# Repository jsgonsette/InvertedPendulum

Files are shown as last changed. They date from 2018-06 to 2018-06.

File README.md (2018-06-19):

# Inverted Pendulum

**Wanna build an inverted pendulum ?** Like in this video :

Pendulum movie (https://www.youtube.com/watch?v=6xe19XnX5L0&t=20s)

you are in the right place. All what you need to known to get an incredible pendulum that jumps and balances is available here. I describe:

* how to make the *electronic board*
* how to make the *shell*
* how to get the *other components*
* how to program the *firmware*
* how to *assemble* the pendulum
* how to connect to the *Control Station software*
* how to *calibrate* the sensors

If you understand french, the long way explanation can be found [on my blog](https://jsgonsette.github.io/). Otherwise, keep reading.

## How to make the electronic board

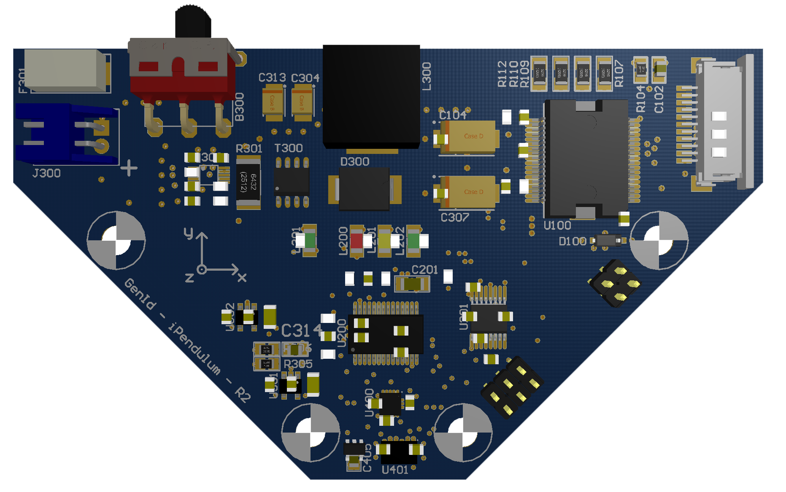
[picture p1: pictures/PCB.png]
Pendulum PCB


### Get the BOM
First, you need all the electronic components on this [BOM list](./Electronic/BOM.xlsx). This kind of components can be found on different sites like:

* [Farnell](http://farnell.com/)
* [RS Components](http://www.rs-online.com/)
* [DigiKey](https://www.digikey.com/)

### Make the PCB
You need to make the PCB whose plans are given by the different files in this [directory](./Electronic/PCB).
(To be continued)

### Soldering of the components

Refer to this [implementation plan](./Electronic/PCB/PCB.PDF) to solder the different components on the both faces. With enough dexterity and patience, all the components could be soldered by hand with a soldering iron. **There are two exceptions**:

* U400 and U401 are only available in LGA package, which means: **no weldable legs !**

You have two options for those ones:

* either you are confident enough to use solder paste and an oven ;
* or you do it like me and you ask your PCB manufacturer to do it for you. This option is ofen available and you can save money by asking them to only solder those two components.

## How to make the shell

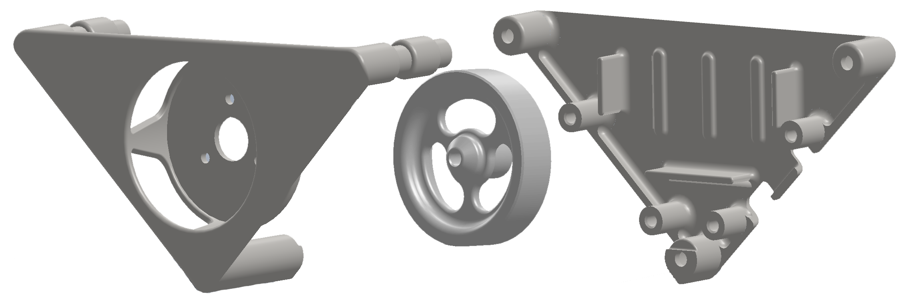
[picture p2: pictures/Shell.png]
Pendulum shell


The shell of the pendulum is composed of three pieces, whose plans are given by the three STEP files in this [directory](./Mecanic/Shell)

* Back of the shell, holding the PCB and the battery
* Front of the shell, holding the motor
* The hub of the flywheel

They have to be 3D printed. You can do it yourself in case you have access to a 3D printer, or just use an online service like [Sculpteo](https://www.sculpteo.com). You need to upload the three STEP files, then to chose this material: [Nylon PA12 (Plastic)](https://www.sculpteo.com/en/materials/plastic-material/). Don't go to other materials, as it could change the weight of the pendulum ; **weight is important!**

## How to get the other components

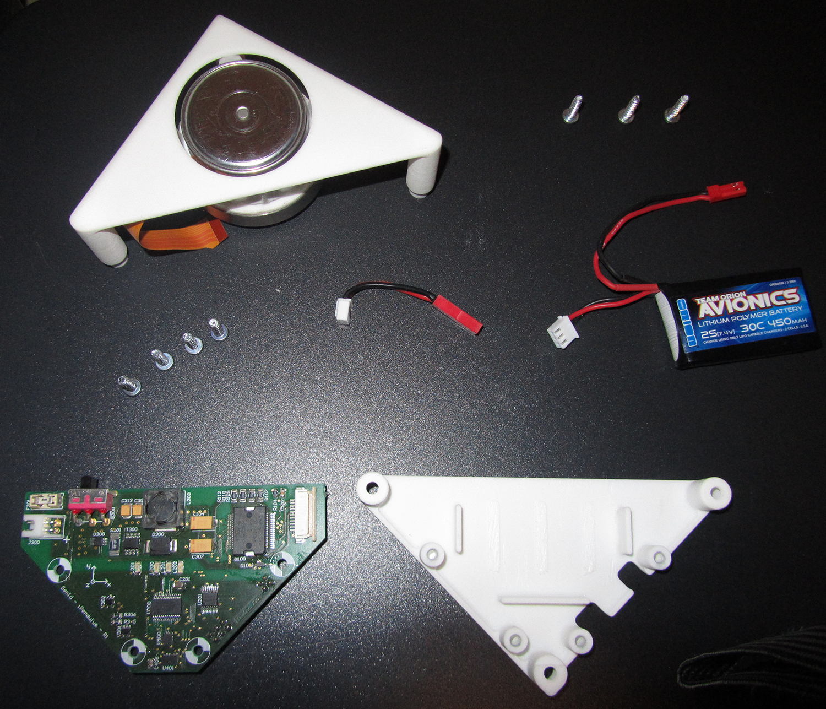
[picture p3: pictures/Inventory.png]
Pendulum inventory


Some additional parts are still needed before getting a functional pendulum.

* The metallic outer ring of the flywheel. It can be ordered on the [Misumi web site](https://uk.misumi-ec.com/). Use the reference **AWSM-D-D55-V48-T10** in the search box to land on the right page.
* The Maxon brushless motor whose reference is [EC45 Flat 200142](https://www.maxonmotor.com/maxon/view/product/200142), available on RS.
* The Lipo battery. The model is not so important, as long as the physical dimensions and the output voltage are respectively: 5x3x1cm and 7.5V. A possible choice can be found [here](https://www.guixmodel.fr/modelisme/accus-et-chargeurs/accus/lipo-2s/accu-lipo-450mah-2s-30c-kryptonium-detail).
* Seven screws to atttach the PCB in the shell and to tie the two parts of the shell together. Check this [Assembly BOM](Assembly%20BOM.xlsx).
* Three screws to attache the motor in the shell. Check this [Assembly BOM](Assembly%20BOM.xlsx).
* The cable to connect the PCB to the battery. You have to assemble it yourself. Check this [Cables BOM](./Mecanic/Cables%20BOM.xlsx).
* The cable to connect the pendulum to the PIC microcontroller programmer. You have to assemble it yourself. Check this [Cables BOM](./Mecanic/Cables%20BOM.xlsx).
* A Lipo charger. Personnaly, I'm very pleased with the [Graupner UltraMat 14 plus](https://www.graupner.de/mediaroot/files/6464_Ultramat_14_plus_de_en_fr_it.pdf) but there are many other ones.
* A Microchip programmation device like the [PICkit 3](https://www.microchip.com/Developmenttools/ProductDetails/PG164130) or the [ICD 3](https://www.microchip.com/Developmenttools/ProductDetails/DV164035), availabe on Farnell, for example.
* (optional) The cable to connect the pendulum to a serial cable. You have to assemble it yourself. Check this [Cables BOM](./Mecanic/Cables%20BOM.xlsx).
* (optional) a USB - Serial cable

## How to program the firmware

The brain of the pendulum is a small Microchip 16bits µC. You must load the right firmware inside to give life to the pendulum.

* Download and install [Microchip MPLAB X](http://microchipdeveloper.com/ipe:installation)
* Connect your chip programmer (like the PICkit 3 or the ICD 3) to the electonic board P200 connector with the dedicated cable
* Connect your chip programmer to your computer
* Charge the Lipo battery and connect it to the electronic board
* Power up the electronic board by switching the power button: the green L301 LED should turn on
* Launch the application **MPLAB IPE**
* (1) In the *device family* field, select **16-bit DSCs (dsPIC33)**
* (2) In the *device* field, select **dsPIC33EP128MC202**
* (3) Ensure the *tool* field displays the name of your chip programmer correctly
* (4) In the source field, browse your computer to select the **iPendulum.hex** firmware, available [here](./Software/Binaries/Firmware/iPendulum.hex)
* (5) Click on **Connect**
* (6) Click on **Program** to flash the microcontroller
* (7) Click on **Verify** to check the microcontroller content

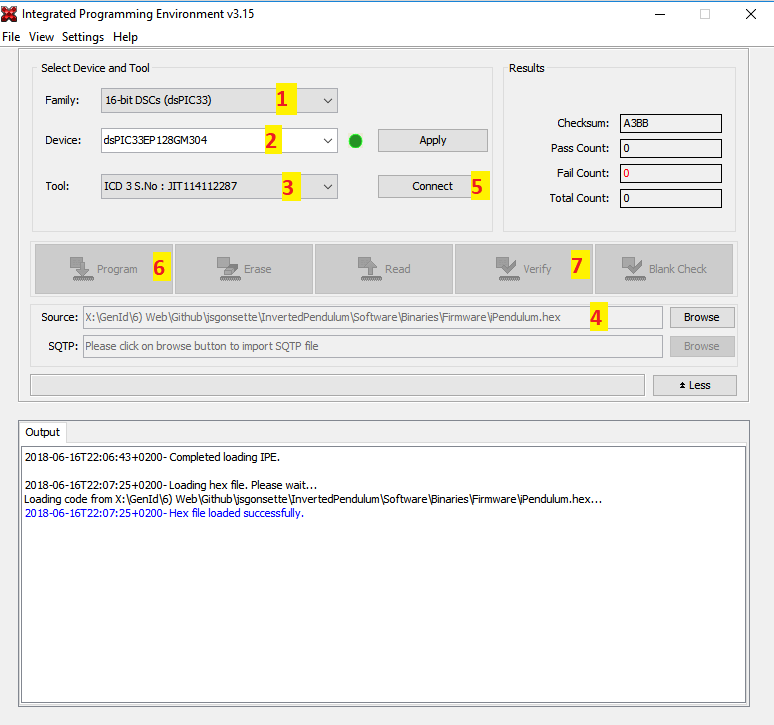
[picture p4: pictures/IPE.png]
Integrated Programming Environment


### Test your flashed electronic board

You can easily check your PCB is fully functional by proceeding as follows:

* Connect the motor to the PCB by inserting its electrical flat ribbon inside the J100 socket, connectors facing down (see picture below)
* Connect the charged Lipo to the PCB
* Hold the motor in your hand firmly, but it must be able to turn freely
* Switch the power button B300 on

If everything is OK, the motor will turn briefly and stop. The red error LED L200 should **NOT** turn on or blink. The meaning of this LED is as follows:

* **Simple** blink: Lipo state of charge too low
* **Double** blink: Motor not detected
* **Tripple** blink: Could not intialize the gyro device
* **Quadruple** blink: Could not initalize the accelerometers device

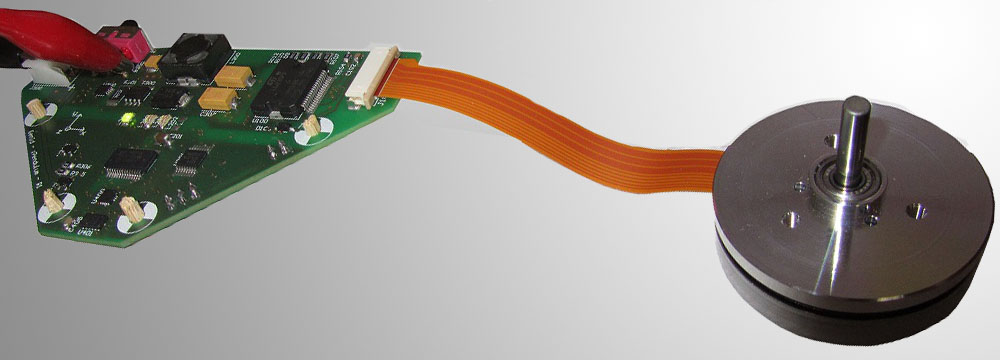
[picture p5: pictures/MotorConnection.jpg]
Testing the PCB


## How to assemble the pendulum

Pendulum shell

* Plug the power cable to the J300 connector on the PCB
* Use four plastic screws to mount the PCB into the back of the shell
* Use the three M3 screws to mount the motor into the front of the shell. **Pay attention** to the orientation of the flat ribbon cable.

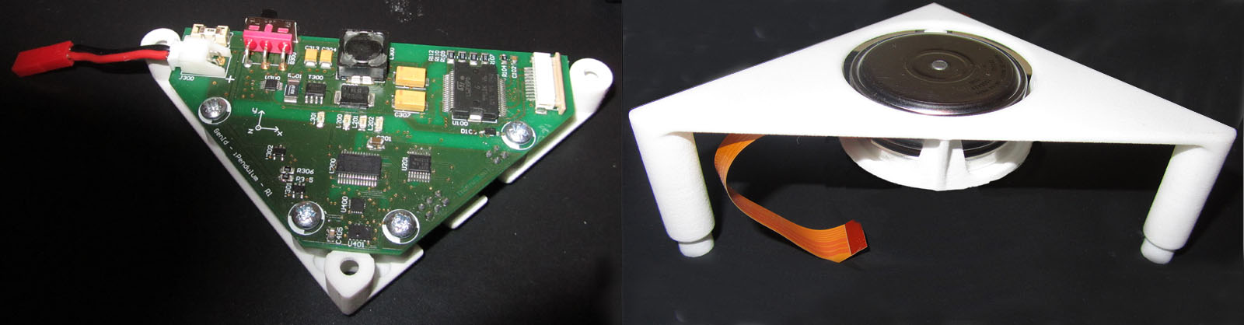
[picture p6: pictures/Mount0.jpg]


* Mount the metallic ring around the plastic flywheel hub. It should be reasonably tight. I had to use a clamping vice.
* Drill a 4mm hole through the axis of rotation of the flywheel hub. 
    * **Test your drill bit** in a stuck of wood before.
    * Use a **drill column** for the hole to be **straight**
* Plug the flywheel on the motor. 
    * **when you push on the flywheel** to get it on the axis, be sure to apply a **vertical force** so as not to **bend the motor**
    * The flywheel should **not** be able to **slip** around the axis: use a bit of strong glue if needed.
* Insert the motor electrical ribbon cable in the PCB connector, connectors facing down.

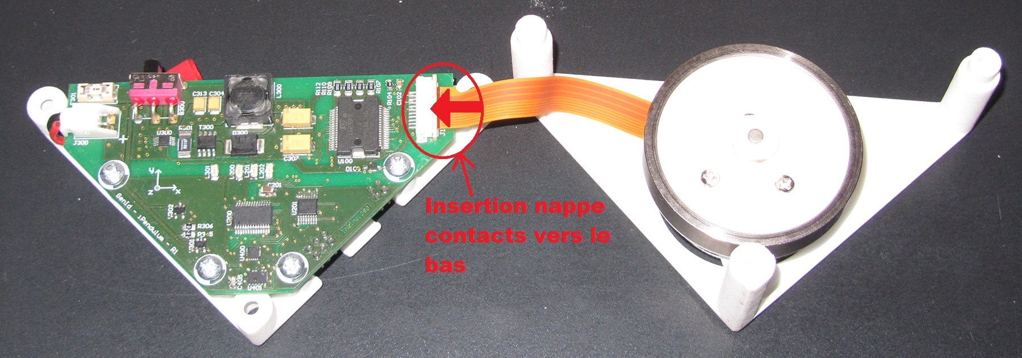
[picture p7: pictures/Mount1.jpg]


* Assemble the two parts of the shell together and fix them with the three remaining screws.
* Put the Lipo battery in place and plug it to the power connector.

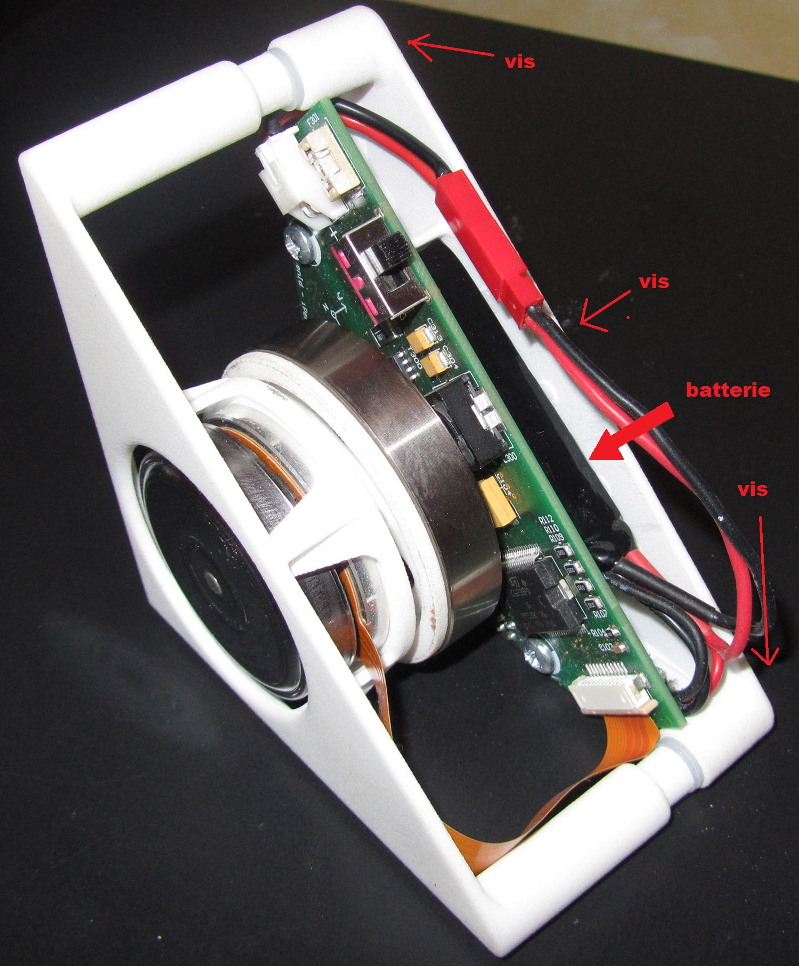
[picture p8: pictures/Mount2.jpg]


## How to connect to the Control Station software

The [Control Station](./Software/Binaries/ControlStation/iPendulumCS.exe) is a small program written in C# (tested on Windows only) enabling to connect to the pendulum through a serial connection. 

* Connect a USB-Serial cable to your computer
* Connect the adapter cable to the USB-Serial cable and to the pendulum
* Launche the Control Station Software
* Select the menu `Tools->Connect to iPendulum`
* Selecting the COM port corresponding to your USB-Serial cable
* Power on the pendulum

You should get to something like on this picture:

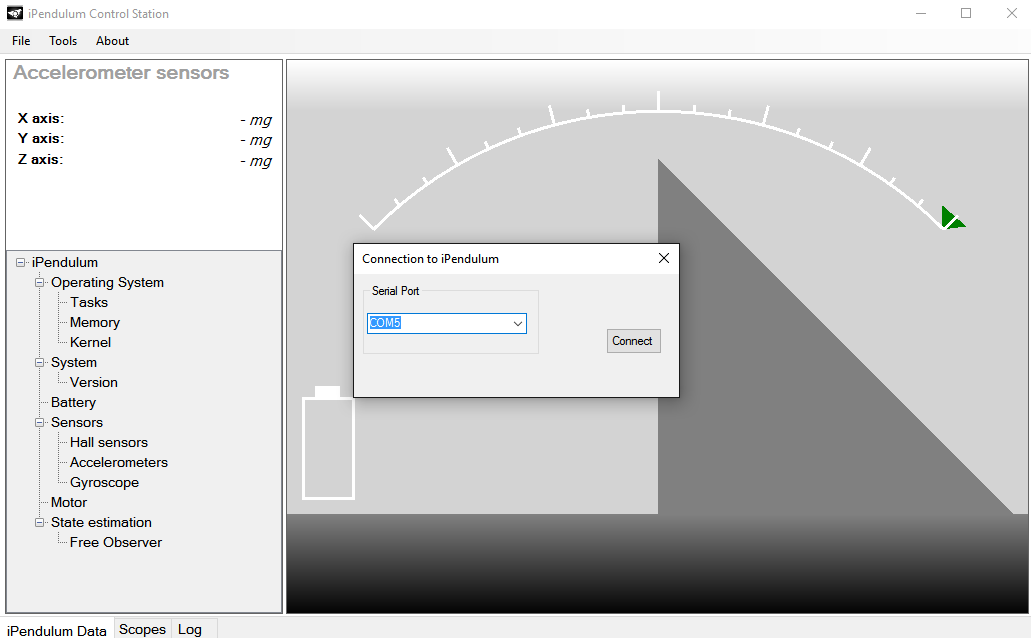
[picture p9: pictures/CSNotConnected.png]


By clicking the `Connect` button, the software testes the communication by sending a request to the pendulum and check the response. If valid, the screen will be displayed in color and the drawing of the pendulum will follow the real pendulum movement.

The panel on the left let you see all the different variables of the running firmware, being related to the OS or to the pendulum sensors.

A thumb in the bottom of the screen makes the view switch to different graphs showing all the telemetries. They correspond to the different sensors measured on the pendulum.

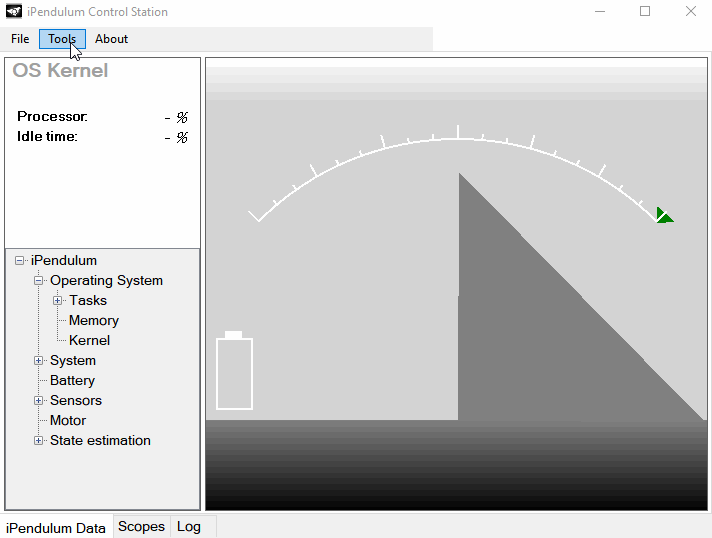
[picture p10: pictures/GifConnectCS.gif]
Connection to the pendulum


## How to calibrate the sensors

Calibration of the pendulum is saved in the flash memory of the microcontroller where it survives even when the pendulum is switech off. The Control Station software helps you to calibrate:

* The measured voltage of the Lipo: `Tools->Calibration->Battery`
* The measured angle of the pendulum `Tools->Calibration->IMU`

Battery voltage calibration only ask you to enter the real voltage of the Lipo, measured with a voltmeter. For the IMU, the software will ask you to put the pendulum in a succession of different positions. Just follow the instructions until the end of the procedure.

You can check the result of this calibration by posing the pendulum on its right of left side, on a flat table, and by checking in the interface that the angle is close to +45° and -45°. This measure can be seen on `State estimation` field of the left panel.

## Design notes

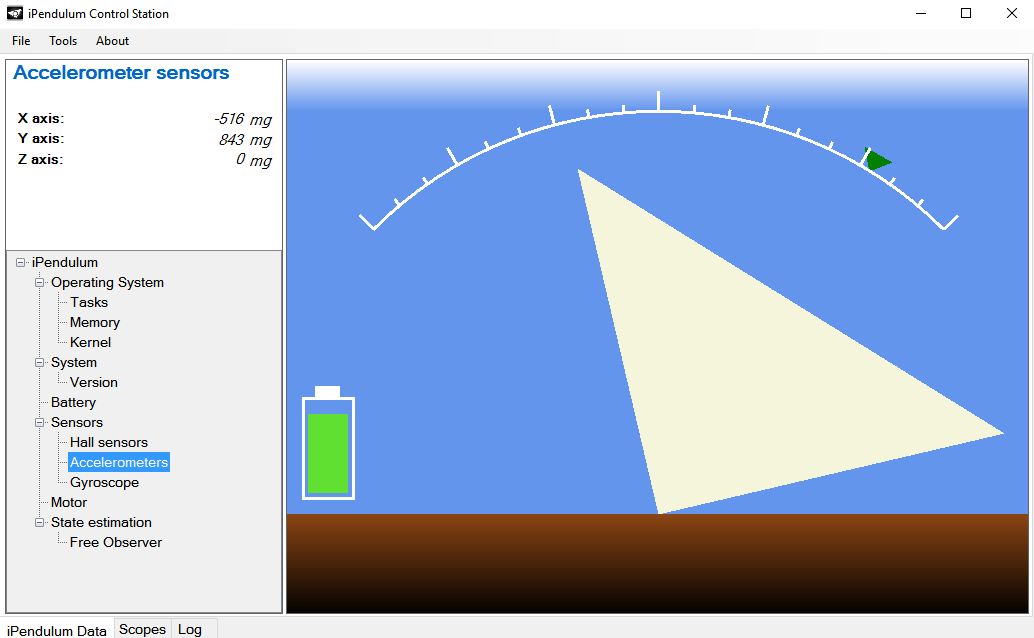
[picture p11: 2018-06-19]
pictures/CSConnected.png

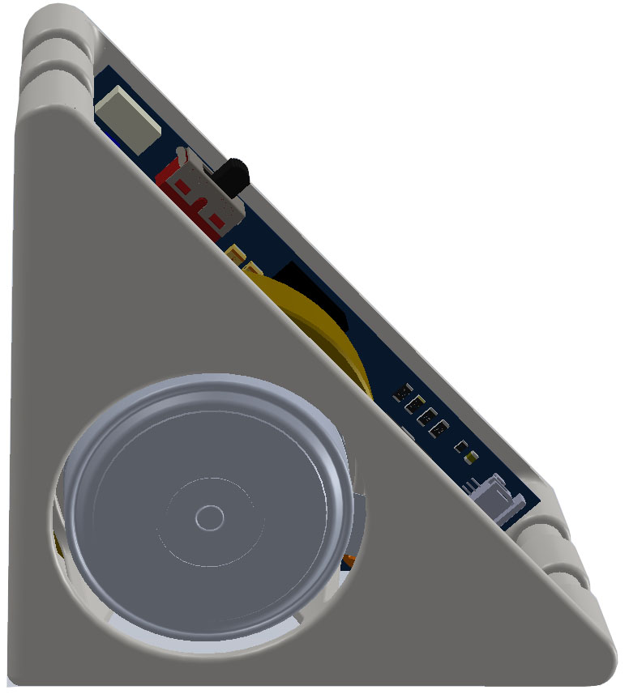
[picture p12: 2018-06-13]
Software/Sources/ControlStation/iPendulumCS/Resources/Front-Right.jpg

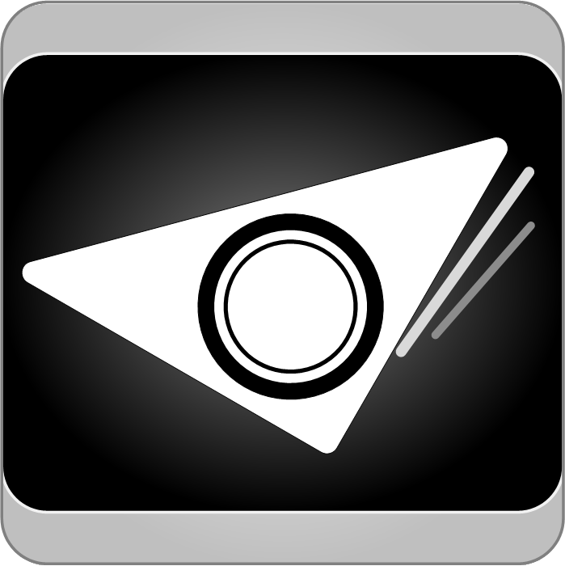
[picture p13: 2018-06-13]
Software/Sources/ControlStation/iPendulumCS/Resources/Pendulum.png

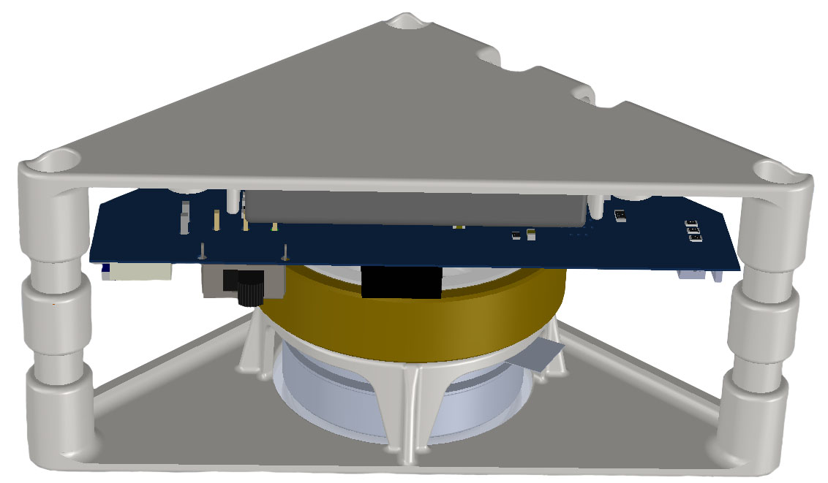
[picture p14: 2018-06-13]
Software/Sources/ControlStation/Resources/Front-Down.jpg

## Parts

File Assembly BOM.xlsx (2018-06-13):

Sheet: Title
Project: | iPendulum
Subject: | Master BOM
Written by |  | Date and Signature
Jean-Sébastien Gonsette
Checked by
/
Approved by
 |  | iPendulum |  |  | GenId SPRL
 |  | Master BOM |  |  | Rue Florent Laurent, 37C
 |  | DWG NO | GENID_DRW_PENDULUM_#9000 |  | 7080 La Bouverie
 |  | Size: A4 | Revision: | 1 | Belgium

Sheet: BOM
 | Component list |  | Master BOM
 | Project: |  | iPendulum
 | Drawing Number: |  | GENID_DRW_PENDULUM_#9000
 | Revision: |  | 1
 | Issue Date: | 2015-03-24
# | Designator | Reference | Manufacturer | Description | Comment | Quantity
2 | P1 | #9001 | GenId | Assembled PCB |  | 1
3 | B1 | 7,4V Lipo 2S 30C 450mah | TeamOrion | Battery |  | 1
4 | C1 | #9002A | GenId | Battery cable |  | 1
5 | M1 | 200142 | Maxon | EC 45 flat Ø42.9 mm, brushless, 30 Watt, with Hall sensors |  | 1
6 | S1 | #8002B | GenId | Shell - PCB |  | 1
7 | S2 | #8002A | GenId | Shell - Motor |  | 1
8 | W1 | #8002C | GenId | Reaction wheel axle |  | 1
9 | W2 | AWSM-D-D55-V48-T10 | Misumi | Reaction wheel ring | D.E.:55mm, D.I.: 48mm, E:10mm | 1
10 | V1, V2, V3, V4, V5, V6, V7 | 452006050081FA | NettleFolds | VIS NO6X1/2 PQ100 |  | 7
11 | V7, V8, V9 | M36 KRSTMCZ100 | Duratool | Screw, Pozi, CSK, Steel, BZP, M3X6 |  | 3
Approved |  |  | Notes |  |  | 18

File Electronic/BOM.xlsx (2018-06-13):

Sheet: Title
Project: | iPendulum
Subject: | PCB BOM
Written by |  | Date and Signature
Jean-Sébastien Gonsette
Checked by
/
Approved by
 |  | iPendulum |  |  | GenId SPRL
 |  | BOM |  |  | Rue Florent Laurent, 37C
 |  | DWG NO | GENID_DRW_PENDULUM_#1001 |  | 7080 La Bouverie
 |  | Size: A4 | Revision: | 2 | Belgium

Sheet: Part List Report
 | Component list
 | Project: |  | iPendulum
 | Drawing Number: |  | GENID_DRW_PENDULUM_#1001
 | Revision: |  | 2
 | Issue Date: | 24/03/2015 | 21:19:57
# | Designator | Reference | Manufacturer | Description | Footprint | Comment | Quantity
1 | B300 | 1101M2S3ABE2 | C&K | SPDT, RIGHT ANGLE, PC THRU-HOLE, Horizontal Actuation | C&K SPDT HORZ 90 |  | 1
2 | C100 | C0805C562K5RA | Kemet | 5.6n-0805-50V-10%-X7R | 0805-CAP |  | 1
3 | C101, C106, C203, C205, C305, C311, C402 | C0805C103K5RA | Kemet | 10n-0805-50V-10%-X7R | 0805-CAP |  | 7
4 | C102 | C0805C122K5RA | Kemet | 1.2n-0805-50V-10%-X7R | 0805-CAP |  | 1
5 | C103 | C0805C333K5RA | Kemet | 33n-0805-50V-10%-X7R | 0805-CAP |  | 1
6 | C104, C307 | T520D686M016ATE050 | Kemet | 68u-16V-20%-0.050R | SMD KEMET D |  | 2
7 | C105, C107, C303 | C0805C224K5RA | Kemet | 220n-0805-50V-10%-X7R | 0805-CAP |  | 3
8 | C200, C202, C204, C206, C207, C208, C209, C210, C309, C314 | C0805C104K5RA | Kemet | 100n-0805-50V-10%-X7R | 0805-CAP |  | 10
9 | C201, C306, C312 | C1206C106K4RA | Kemet | 10u-1206-16V-10%-X7R | 1206-CAP |  | 3
10 | C300, C400, C403, C404, C405 | C0805C104K8RA | Kemet | 100n-0805-10V-10%-X7R | 0805-CAP |  | 5
11 | C301, C302, C310, C401 | C0805C105K4RA | Kemet | 1u-0805-16V-10%-X7R | 0805-CAP |  | 4
12 | C304, C313 | T520B476M010ATE035 | Kemet | 47u-10V-20%-0.035R | SMD KEMET B |  | 2
13 | C308 | C0805C101J5GA | Kemet | 100p-0805-50V-5%-C0G | 0805-CAP |  | 1
14 | D100, D101 | 1N4148W | Diodes Incorporated | SURFACE MOUNT FAST SWITCHING DIODE | SOD-123 |  | 2
15 | D300 | MBRS340T3 | ON SemiConductor | Surface Mount Schottky Power Rectifier | SMC-403 |  | 1
16 | F301 | 0448 008. | Littelfuse | 8A-125V | SMF Omni-Blok |  | 1
17 | J100 | 52271-1179 | Molex | 11 way, 1.00mm Pitch FFC/FPC Connector, Right Angle, Contact Bottom, SMT, ZIF | FPC_11x1_Bottom |  | 1
18 | J200 | 90131-1082 | Molex | 2.54mm Pitch C-Grid III Header, Dual Row, Vertical, 4 Circuits, 0.38m Gold (Au) | C-GRID3-2x2 |  | 1
19 | J300 | S2B-XH-A | JST | XH 2 ways Disconnectable Crimp style connectors | S2B-XH-A |  | 1
20 | L200 | KP-3216EC | Kingbright | LED, SMD, 1206, RED | 1206-LED-RED |  | 1
21 | L201 | KP-3216YC | Kingbright | LED, SMD, 1206, YELLOW | 1206-LED-YELLOW |  | 1
22 | L202, L301 | KP-3216SGC | Kingbright | LED, SMD, 1206, GREEN | 1206-LED-GREEN |  | 2
23 | L300 | SRR1206-5R0ML | Bourns | Shielded High Power Inductor - 5.0uH | BOURNS-SRR1206 |  | 1
24 | P200 | 90131-0763 | Molex | 2.54mm Pitch C-Grid III Header, Dual Row, Vertical, 6 Circuits, 0.38m Gold (Au) | C-GRID3-2x3 |  | 1
25 | R100 | CRCW080556K0FKEA | Vishay | 56K-0805-0.125W-1%-100ppm | SMD 0805 |  | 1
26 | R101 | CRCW0805100KFKEA | Vishay | 100K-0805-0.125W-1%-100ppm | SMD 0805 |  | 1
27 | R102 | CRCW08051K00FKEA | Vishay | 1K-0805-0.125W-1%-100ppm | SMD 0805 |  | 1
28 | R103 | CRCW080511K0FKEA | Vishay | 11K-0805-0.125W-1%-100ppm | SMD 0805 |  | 1
29 | R104, R305 | CRCW080520K0FKEA | Vishay | 20K-0805-0.125W-1%-100ppm | SMD 0805 |  | 2
30 | R105, R302 | CRCW080524K9FKEA | Vishay | 24.9K-0805-0.125W-1%-100ppm | SMD 0805 |  | 2
31 | R106 | CRCW1206100RFKEA | Vishay | 100R-1206-0.25W-1%-100ppm | SMD 1206 |  | 1
32 | R107, R109, R110, R112 | CRCW12061R00FKEA | Vishay | 1R-1206-0.25W-1%-100ppm | SMD 1206 |  | 4
33 | R108, R111, R113 | CRCW08054K70FKEA | Vishay | 4.7K-0805-0.125W-1%-100ppm | SMD 0805 |  | 3
34 | R200, R306 | CRCW080510K0FKEA | Vishay | 10K-0805-0.125W-1%-100ppm | SMD 0805 |  | 2
35 | R201 | CRCW0805330RFKEA | Vishay | 330R-0805-0.125W-1%-100ppm | SMD 0805 |  | 1
36 | R202, R203, R204, R304 | CRCW0805130RFKEA | Vishay | 130R-0805-0.125W-1%-100ppm | SMD 0805 |  | 4
37 | R300 | CRCW0805160KFKEA | Vishay | 160K-0805-0.125W-1%-100ppm | SMD 0805 |  | 1
38 | R301 | WSL2512R0150FEA | Vishay | 15m-2512-1W-1% | SMD 2512 |  | 1
39 | R303 | CRCW0805215KFKEA | Vishay | 215K-0805-0.125W-1%-100ppm | SMD 0805 |  | 1
40 | T300 | FDS6680AS | Fairchild | 30V N-Channel PowerTrench SyncFET | SOIC_8 |  | 1
41 | U100 | L6235 | ST | DMOS driver for 3-phase brushless DC motor | POWSO_36_Hole |  | 1
42 | U200 | dsPIC33EP128MC202 | Microchip | 16-Bit Microcontrollers and Digital Signal Controllers with High-Speed PWM, Op Amps and Advanced Analog | SSOP_28 |  | 1
43 | U201 | SN65C3221E | Texas Instruments | 3-V TO 5.5-V SINGLE-CHANNEL RS-232 1-Mbit/s LINE DRIVER/RECEIVER | SSOP_16 |  | 1
44 | U300 | MAX668 | Maxim Integrated | 1.8V to 28V Input, PWM Step-Up Controllers in µMAX | µMAX |  | 1
45 | U301 | LP2985-33 | Texas Instruments | 150-mA Low-Noise Low-Dropout Regulator With Shutdown | SOT-23 |  | 1
46 | U302 | LP2992-33 | Texas Instruments | Micropower 250mA Low-Noise Ultra Low-Dropout Regulator | SOT-23 |  | 1
47 | U400 | ISZ-2510 | InvenSense | Single-chip, digital output, single axis MEMS gyroscope | QFN-16 |  | 1
48 | U401 | ADXL345 | Analog Devices | 3-Axis, ±2 g/±4 g/±8 g/±16 g Digital Accelerometer | LGA-14 |  | 1
49 | U402 | SN74AHC1G32 | Texas Instrument | Single 2 input Positive Or Gate | DBV |  | 1
Approved |  |  | Notes |  |  |  | 90

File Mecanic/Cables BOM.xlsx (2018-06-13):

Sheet: Title
Project: | iPendulum
Subject: | Cables BOM
Written by |  | Date and Signature
Jean-Sébastien Gonsette
Checked by
/
Approved by
 |  | iPendulum |  |  | GenId SPRL
 |  | Cables BOM |  |  | Rue Florent Laurent, 37C
 |  | DWG NO | GENID_DRW_PENDULUM_#9002 |  | 7080 La Bouverie
 |  | Size: A4 | Revision: | 1 | Belgium

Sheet: A - Battery Cable
 | Component list |  | Battery Cable
 | Project: |  | iPendulum
 | Drawing Number: |  | GENID_DRW_PENDULUM_#9002
 | Revision: |  | 1
 | Issue Date: | 2014-11-30
# | Designator | Reference | Manufacturer | Description | Comment | Quantity
1 | JP1, JP2 | SYM-001T-P0.6 | JST | RCY connector - Socket pin contact |  | 2
2 | J1 | SYR-02T | JST | RCY connector - Socket housing |  | 1
3 | JP3, JP4 | SXH-001T-P0.6 | JST | XH connector - Plug socket contact |  | 2
4 | J2 | XHP-2 | JST | XH connector - Plug housing |  | 1
5 | W1 |  |  | AWG 20 single wire - red | 40mm | 1
6 | W2 |  |  | AWG 20 single wire - black | 40mm | 1
Approved |  |  | Notes |  |  | 8

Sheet: B - Auxillary Power Cable
 | Component list |  | Auxillary Power Cable
 | Project: |  | iPendulum
 | Drawing Number: |  | GENID_DRW_PENDULUM_#9002
 | Revision: |  | 1
 | Issue Date: | 2014-11-30
# | Designator | Reference | Manufacturer | Description | Comment | Quantity
1 | JP1, JP2 | SYF-001T-P0.6 | JST | RCY connector - Plug socket contact |  | 2
2 | J1 | SYP-02T-1 | JST | RCY connector - Plug housing |  | 1
3 | W1 |  |  | AWG 20 single wire - red |  | 1
4 | W2 |  |  | AWG 20 single wire - black |  | 1
5
6
Approved |  |  | Notes |  |  | 5

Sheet: C - RS232 Cable
 | Component list |  | RS232 Cable
 | Project: |  | iPendulum
 | Drawing Number: |  | GENID_DRW_PENDULUM_#9002
 | Revision: |  | 1
 | Issue Date: | 2014-11-30
# | Designator | Reference | Manufacturer | Description | Comment | Quantity
1 | J1 | M20-1070200 | Harwin | M20-1 Series, 2 rows, 4 contacts |  | 1
2 | JP1-4 | M20-1180046 | Harwin | M20 socket contact |  | 4
3 |  |  |  | Ribbon cable, AWG 28
4
5
6
Approved |  |  | Notes |  |  | 5

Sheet: D - Programmation Cable
 | Component list |  | Programmation Cable
 | Project: |  | iPendulum
 | Drawing Number: |  | GENID_DRW_PENDULUM_#9002
 | Revision: |  | 1
 | Issue Date: | 2014-11-30
# | Designator | Reference | Manufacturer | Description | Comment | Quantity
1 | J1 | M20-1070300 | Harwin | M20-1 Series, 2 rows, 6 contacts |  | 1
2 | JP1-6 | M20-1180046 | Harwin | M20 socket contact |  | 6
3
4
5
6
Approved |  |  | Notes |  |  | 7

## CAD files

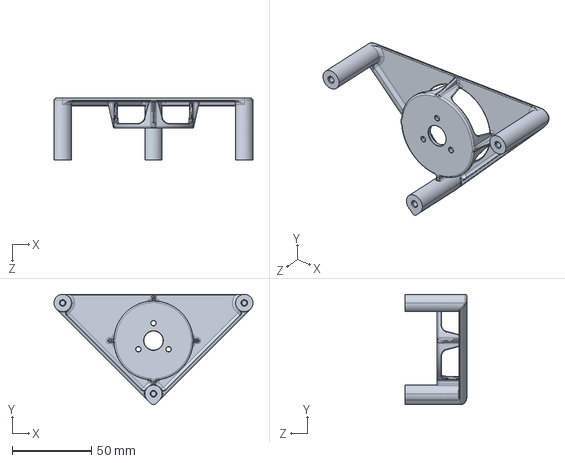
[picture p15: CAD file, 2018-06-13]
Mecanic/Shell/8002A_Shell_Motor.STEP
125.9 x 69.9 x 39.0 mm

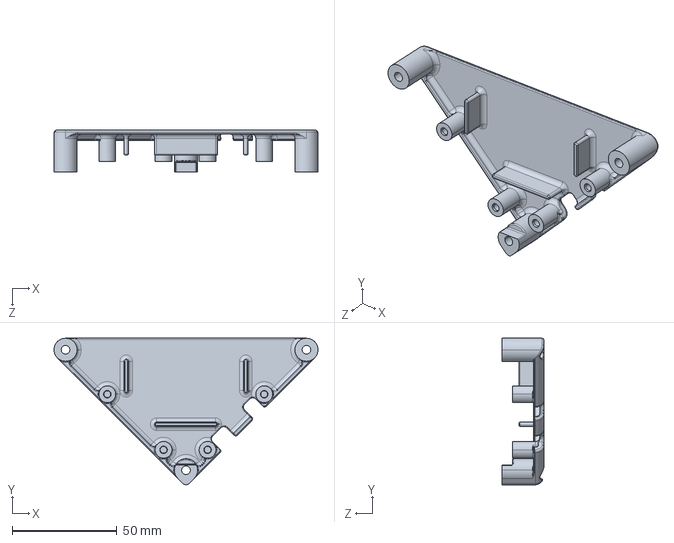
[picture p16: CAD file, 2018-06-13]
Mecanic/Shell/8002B_Shell_PCB.STEP.STEP
125.9 x 69.9 x 20.0 mm

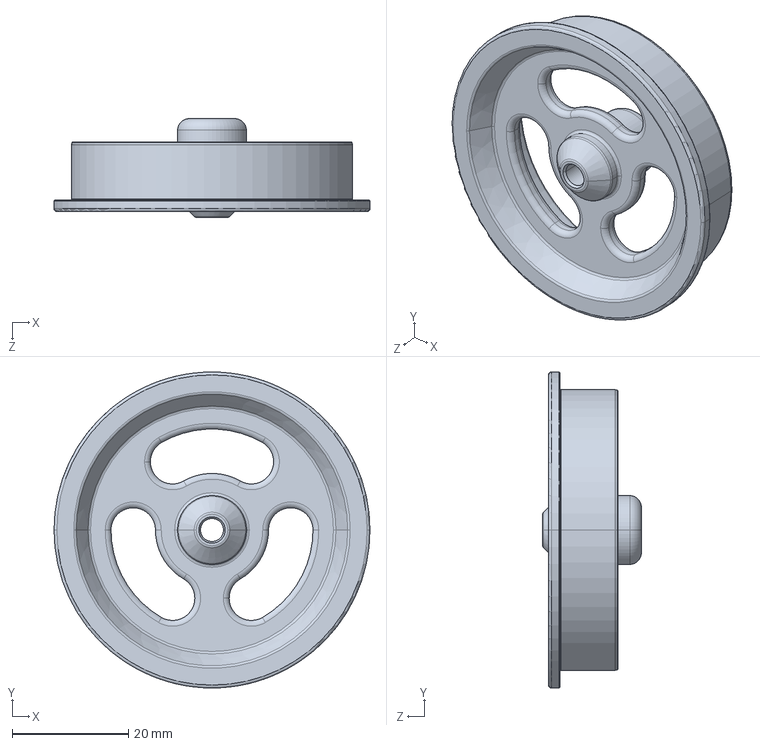
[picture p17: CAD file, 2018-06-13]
Mecanic/Shell/8002C_Wheel_Axle.STEP
54.4 x 54.4 x 17.0 mm

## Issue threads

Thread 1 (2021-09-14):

Programming the Inverted Pendulum

Roy-Salomon, 2021-09-14:
Hello, jsgonsette,
I am from Switzerland and work for an electronics company, in an apprenticeship training department. We saw your idea in a German magazine Elektror. We thought it was a great idea and wanted to copy it. We have all the components and the whole board is assembled. But we still can't program the dsPIC. We get the following error message (see pictures in the attachment):

Target Device ID (0x0) is an Invalid Device ID. Please check your connections to the Target Device. Would you like to continue?

Programmer: Pickit 3
Program MPLAB X v.4.00 (with the .hex file we tried the program: MPLAB IPE v.4.00)
Compiler: XC16 v.1.24

Maybe you can help us further. Thanks for the answer.
Best regards Roy

Closed 2021-09-16.

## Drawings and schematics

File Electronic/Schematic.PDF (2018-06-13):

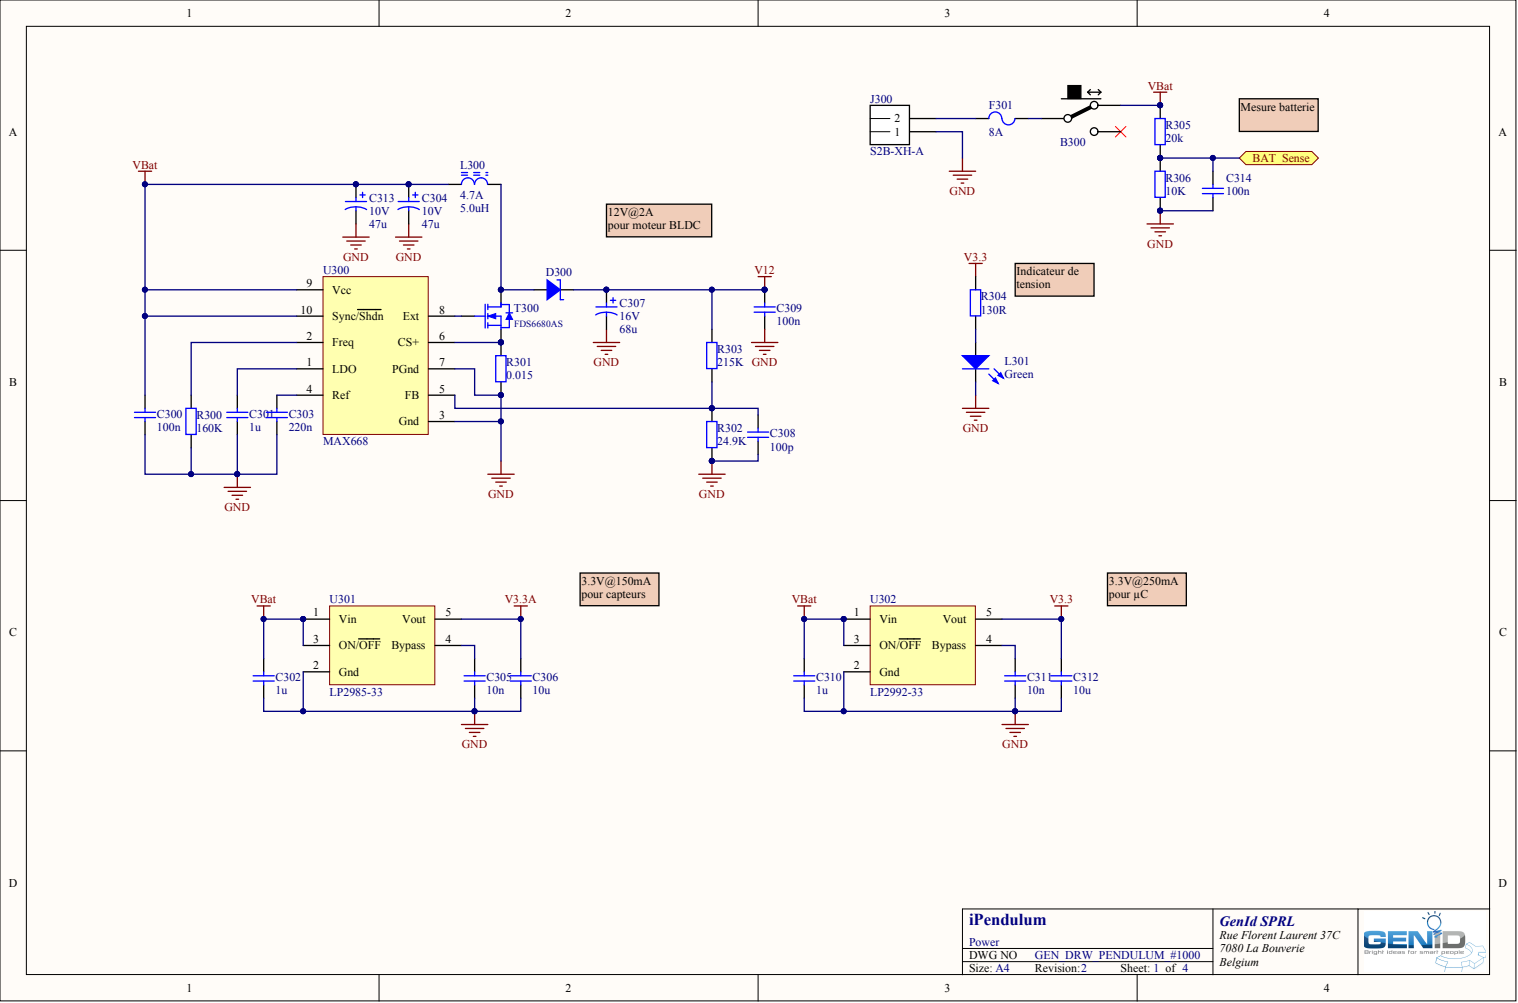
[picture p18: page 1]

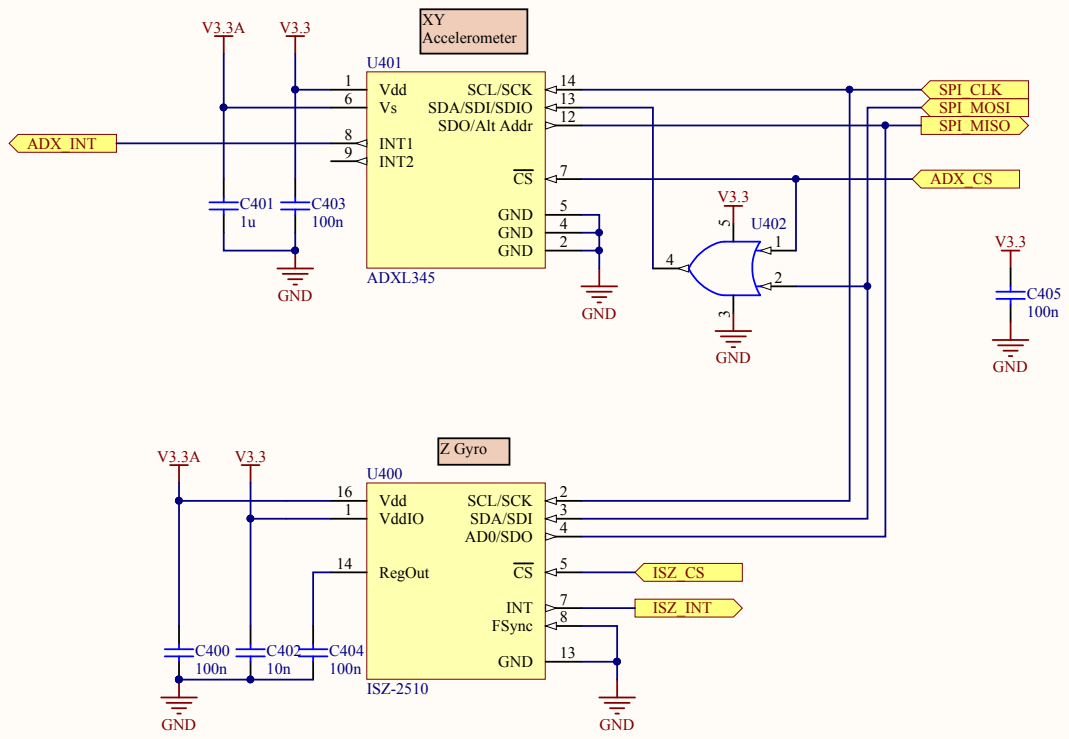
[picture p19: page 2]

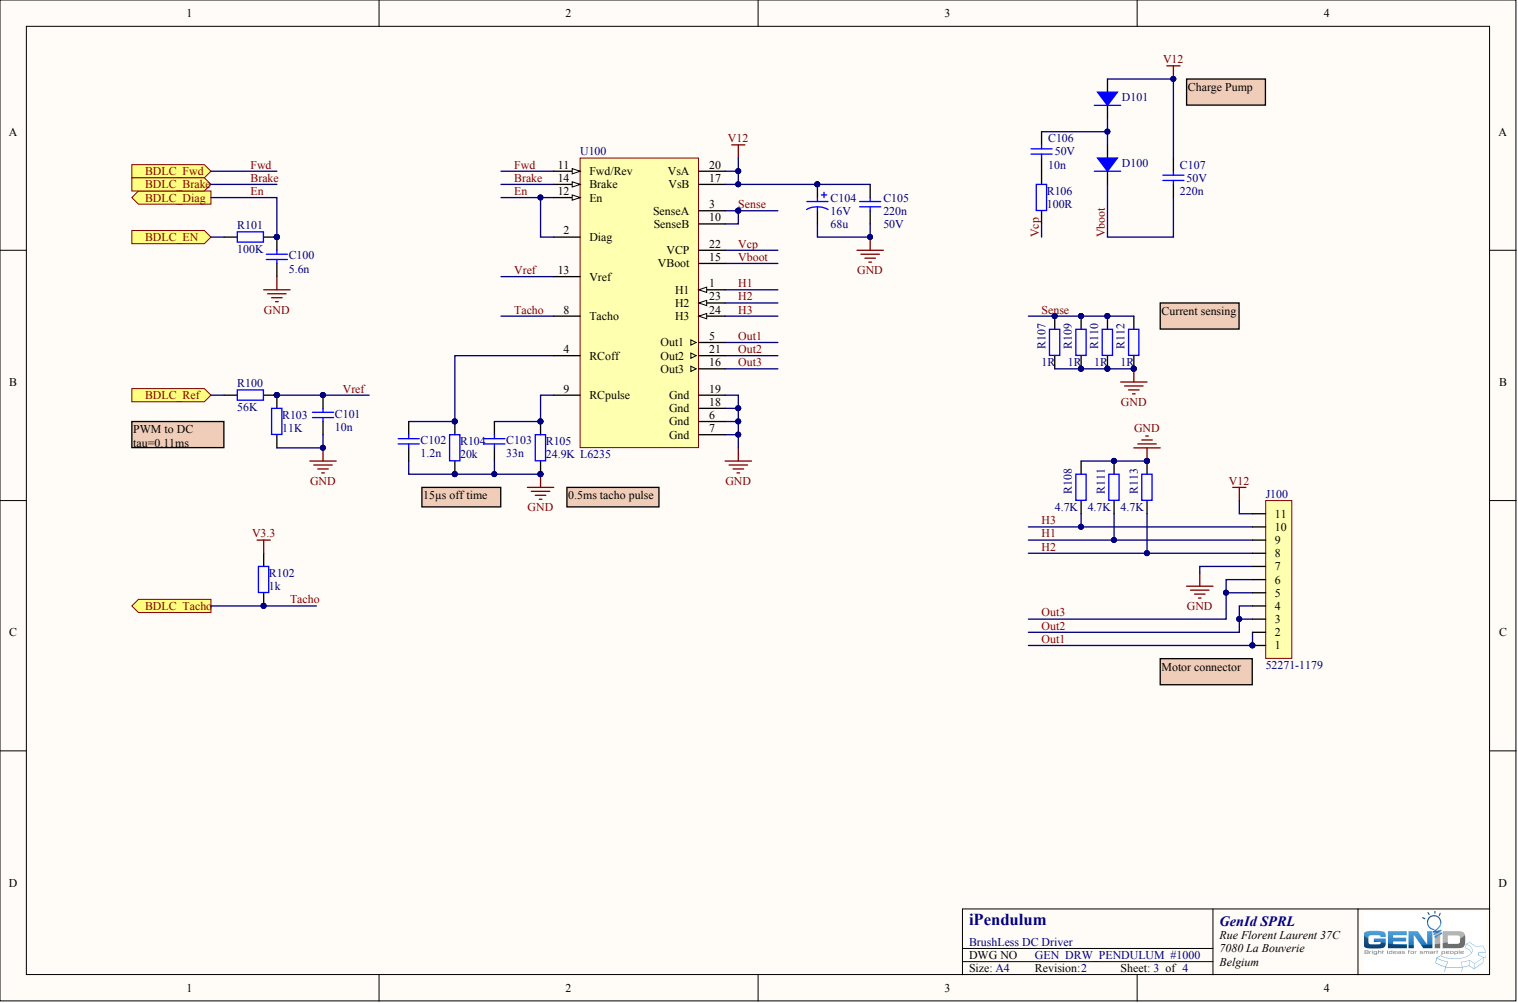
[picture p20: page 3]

H3
H1
H2

Out2
Out1

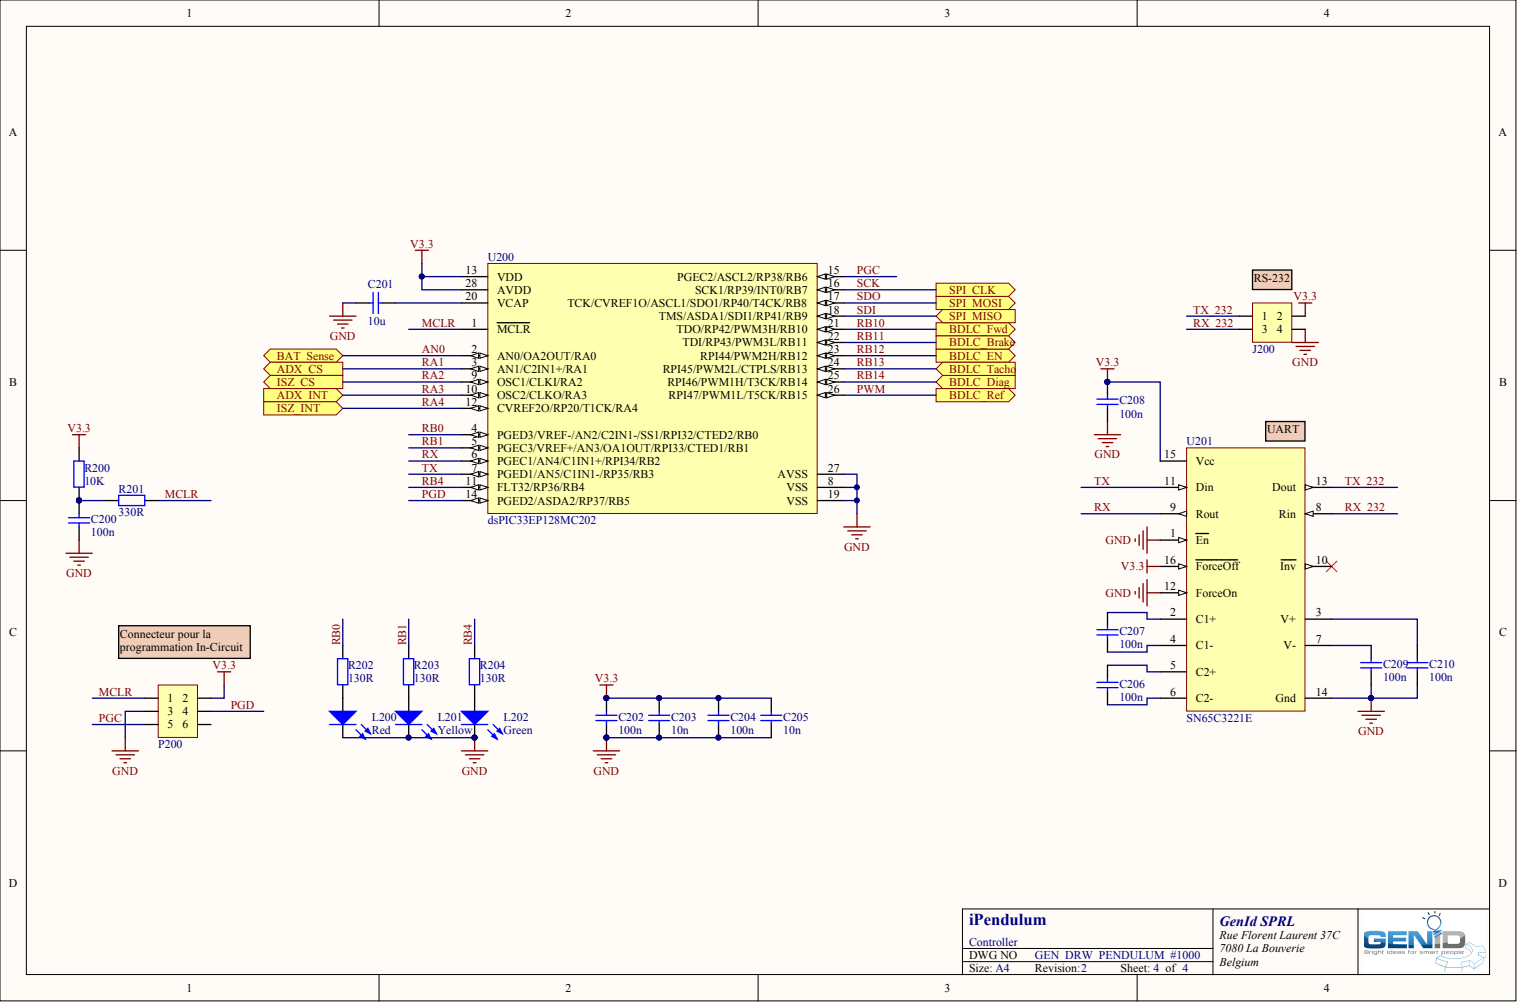
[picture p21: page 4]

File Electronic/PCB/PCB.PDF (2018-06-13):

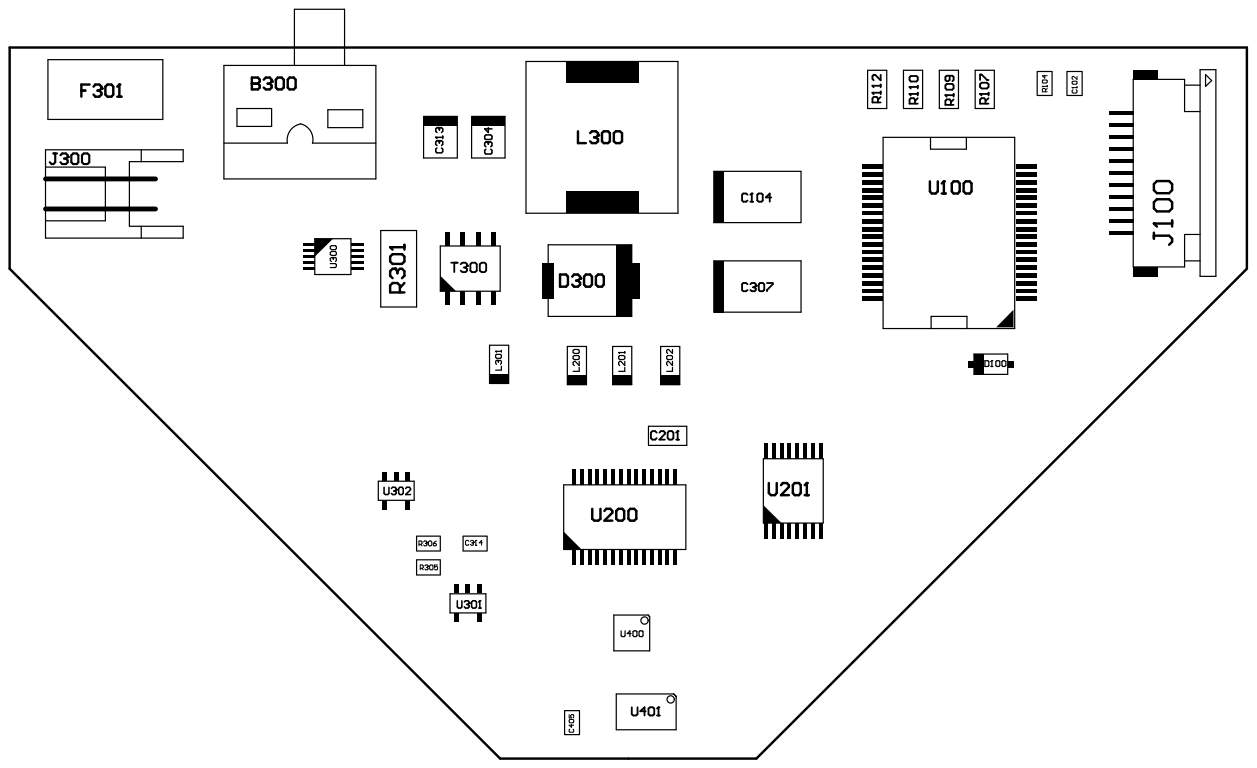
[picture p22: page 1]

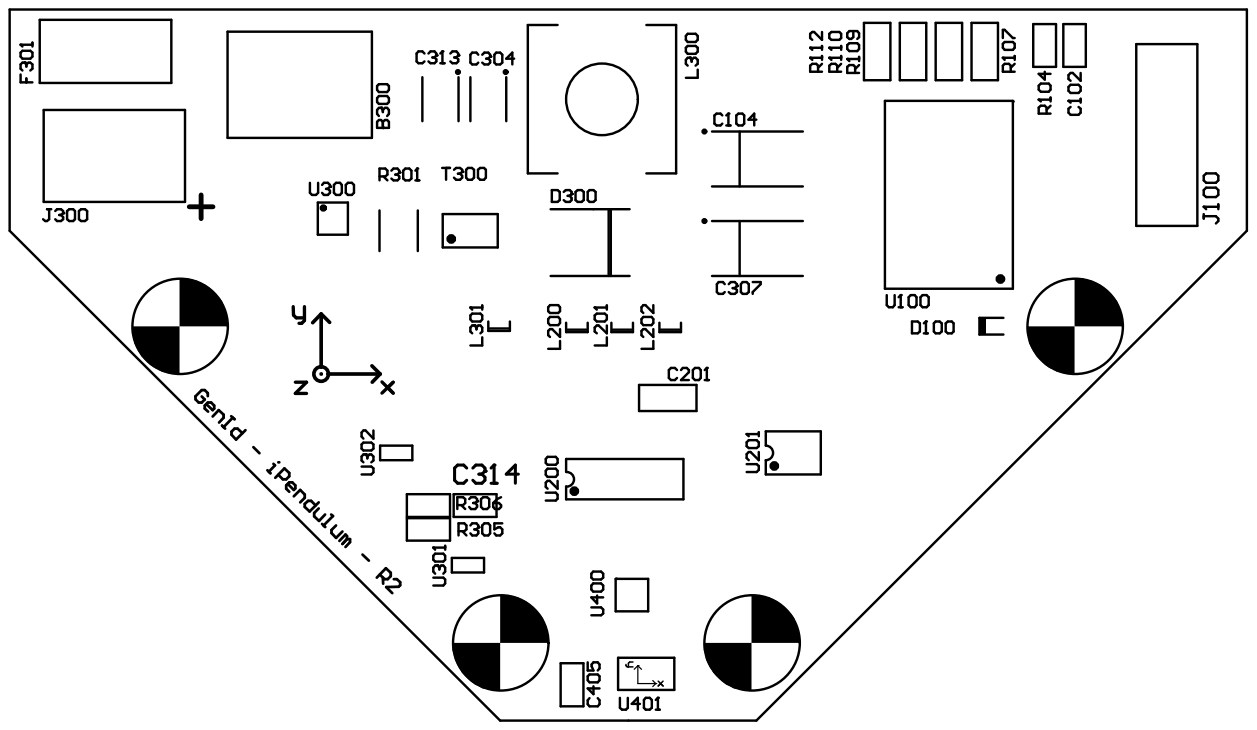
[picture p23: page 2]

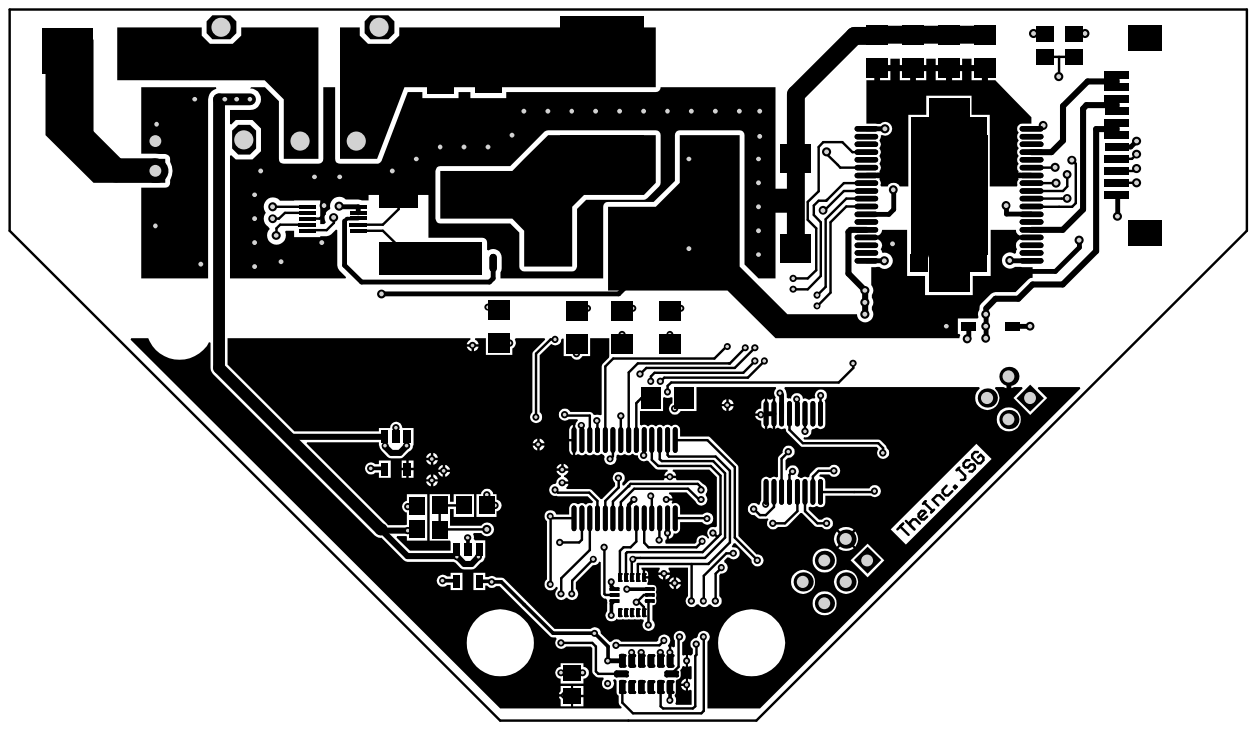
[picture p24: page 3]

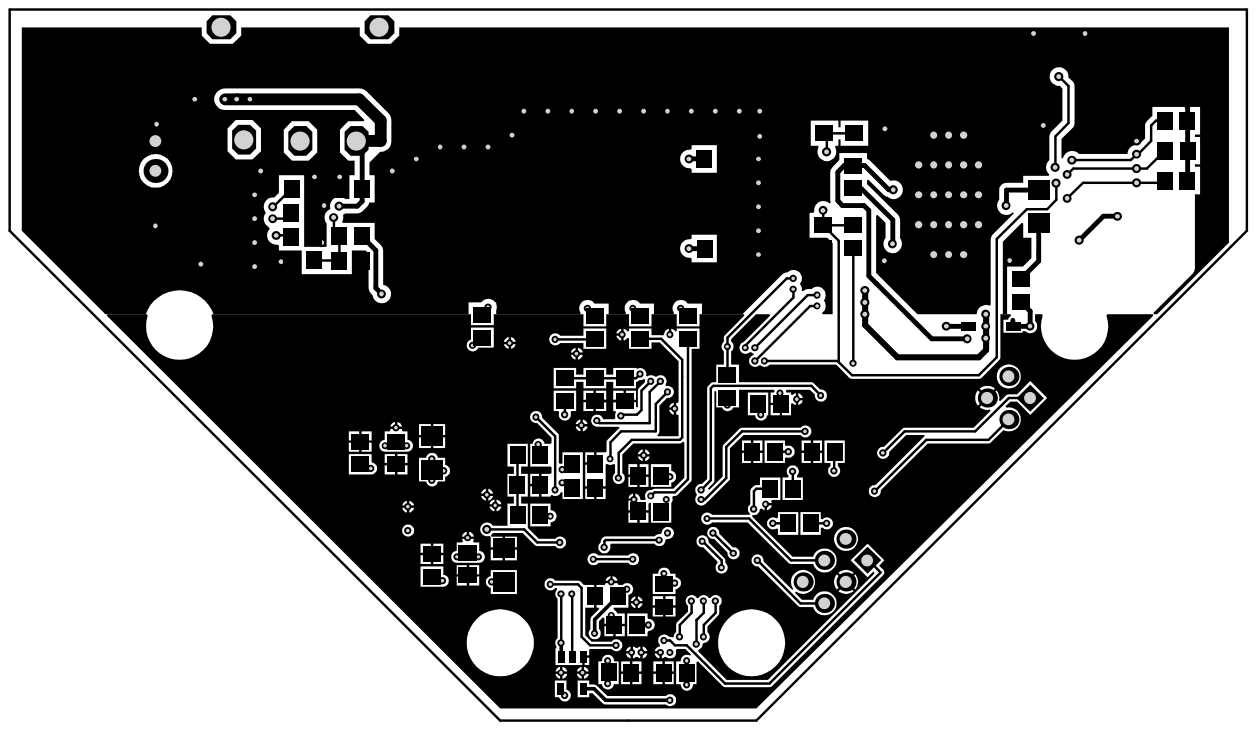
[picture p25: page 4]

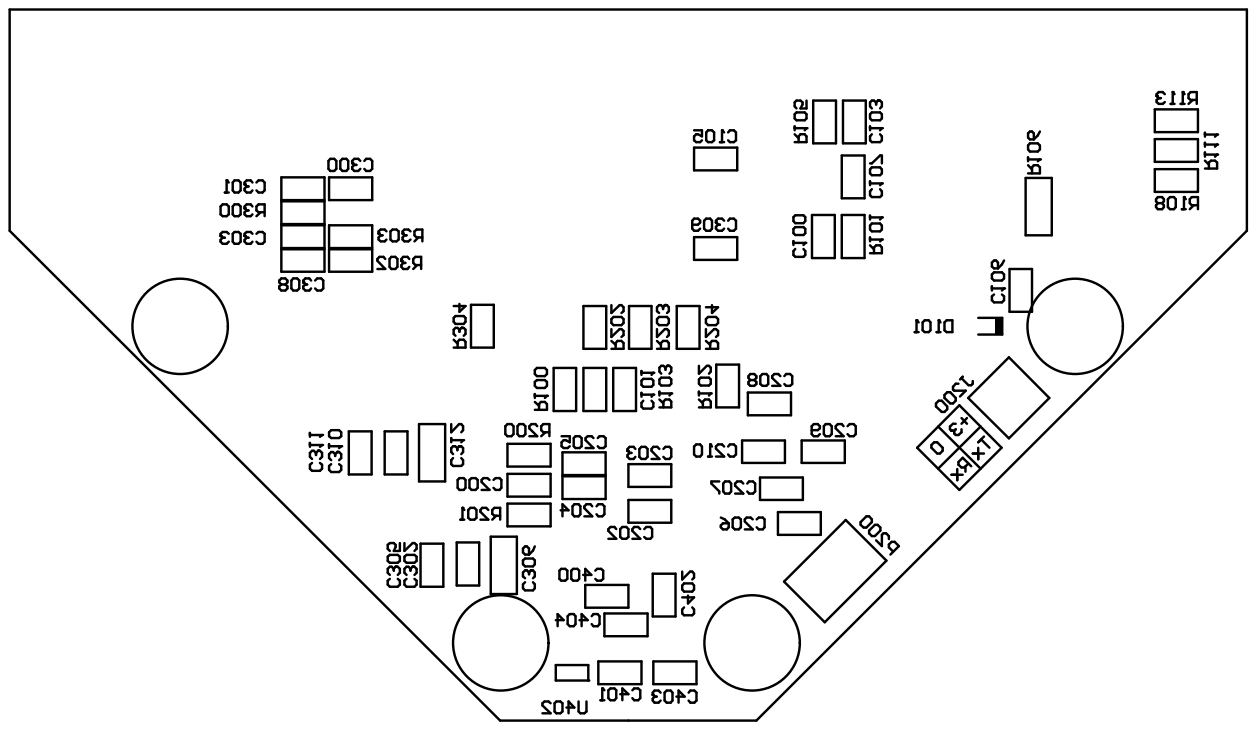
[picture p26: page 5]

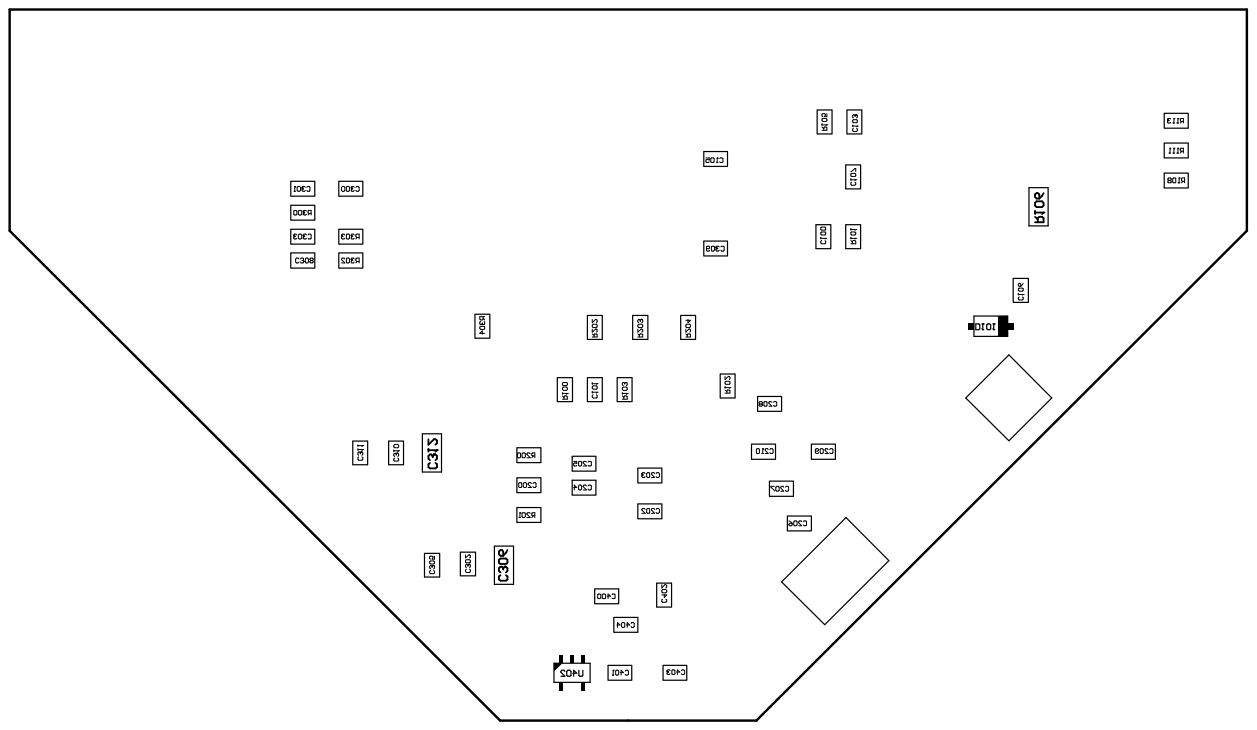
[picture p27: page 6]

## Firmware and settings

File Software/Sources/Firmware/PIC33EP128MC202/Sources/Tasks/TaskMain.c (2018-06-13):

// ###########################################################################
//
// Copyright (C) 2015 GenId SPRL
//
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
#include "BSP.h"
#include "Config.h"
#include "Global.h"
#include "./Tasks/Controller.h"
#include "./Tools/Message.h"
#include "./Tools/PRNG.h"
#include "./Devices/ADXL345.h"
#include "./Devices/ISZ2510.h"
#include "./Tasks/TaskLED.h"
#include "./Tasks/TaskUartTx.h"
#include "./Tasks/TaskMain.h"
#include "./Interfaces/Motor.h"
#include "./Interfaces/Battery.h"


// ===========================================================================
// T Y P E S
// ===========================================================================


// ===========================================================================
// P R I V A T E
// ===========================================================================

/// Application mode
static TMAIN_Mode gs_mode;

/// Telemetry speed (0: stopped)
static int gs_tm;

/// Telemetry counter
static int gs_tmCounter;

/// Config need to be saved
static Bool gs_saveConfig;

/// Telemetries raw buffer
static Byte gs_rawBuffer [200];

/// Circular message buffer for telemetries
static MSG_Buffer gs_tmBuffer;


// ===========================================================================
// P R I V A T E   P R O T O
// ===========================================================================

/// \name Internal functions
//@{
static Word InitApplication ();
static void InitPnrg ();
static void SaveConfig ();
static void SendTelemetry (Dword cycleCounter);
static int TestMotor ();
static int SetupAccelerometer ();
static int SetupGyroscope ();
//@}



// ###########################################################################
//
// P U B L I C
//
// ###########################################################################

// ===========================================================================
// <TMAIN_EntryPoint>
///
/// \brief		Main application task entry point
///
// ===========================================================================
void TMAIN_EntryPoint (void* param)
{
	Word error;
	Dword ms, msNext = 0;
	Dword cycleCount;
	
	// Init application
	error = InitApplication ();
	
	// Show critical error (RED pulses the error number)
	if (error != 0)
	{
		TLED_Off (LED_GREEN);
		TLED_Off (LED_YELLOW);
		TLED_Pulse (LED_RED, error);
		return;
	}
	
//TMAIN_SetMode (MODE_Free);

	// Main loop
	while (1)
	{
		// Wait next controller cycle
		if (CTRL_WaitCycle (DELAY_MS (500), &cycleCount)) 
		{
			// Send telemetries if needed
			if (gs_tm > 0) SendTelemetry (cycleCount);
			
			// Save config if needed
			if (gs_saveConfig) SaveConfig ();
		}
		
		// Check battery level every minute
		ms = GetMsCount ();
		if (ms >= msNext)
		{
			msNext = ms + 60000;
			if (BAT_GetVoltage () < BAT_MIN_VOLTAGE) break;
		}
	}
	
	// No more battery. Stop the pendulum
	SuspendTask (g_taskUartTx);
	SuspendTask (g_taskUartRx);
	CTRL_SetMode (CTRL_Stop);
	
	// Warning
	TLED_Off (LED_GREEN);
	TLED_Off (LED_YELLOW);
	TLED_Pulse (LED_RED, 1);
	
	SleepTask (DELAY_S (10));
	
	// Shut down everything to minimize consumption
	/// \todo
}


// ===========================================================================
// <TMAIN_CalibrateBattery>
///
/// \brief	Calibrate the battery with a new reference voltage
///
/// \param[in]	refVoltage 		Reference voltage measurement [1/100 V]
// ===========================================================================
void TMAIN_CalibrateBattery (Word refVoltage)
{
	BAT_Calibrate (refVoltage);
	gs_saveConfig = True;
}


// ===========================================================================
// <TMAIN_CalibrateIMU>
///
/// \brief	Calibrate the IMU with a new bias and scale factors correction
///
/// \param[in]	accScales		Measured acc scale factorsbias (x, y) [1/1000]
/// \param[in]	accBias			Measured acc bias (x, y, z) [µG]
/// \param[in]	gyroBias		Measured gyro bias [1/1000 °/s]
// ===========================================================================
void TMAIN_CalibrateIMU (Long accScales [2], Long accBias [3], Long gyroBias)
{
	ISZ2510_SetCalibrationOffset (g_ISZ2510, gyroBias);
	
	ADXL345_SetCalibrationOffset (g_ADXL345, 0, (Short) (accBias [0] / 1000));
	ADXL345_SetCalibrationOffset (g_ADXL345, 1, (Short) (accBias [1] / 1000));
	ADXL345_SetCalibrationOffset (g_ADXL345, 2, (Short) (accBias [2] / 1000));
	
	ADXL345_SetCalibrationScaler (g_ADXL345, 0, accScales [0] / 1000.0f);
	ADXL345_SetCalibrationScaler (g_ADXL345, 1, accScales [1] / 1000.0f);
	
	gs_saveConfig = True;
}


// ===========================================================================
// <TMAIN_SetTelemetry>
///
/// \brief	Enable or disable telemetry uploading
///
/// \param[in]	s	0: No telemetry
///					n: Telemetry sent 1 cycle out of n
// ===========================================================================
void TMAIN_SetTelemetry (int n)
{
	EnterCritical ();
	{	
		gs_tm = n;
		gs_tmCounter = 0;

		// Configure the controller if needed: it cannot be stopped
		// if we have to send the telemetries
		if (gs_mode == MODE_Stop)
		{
			if (gs_tm > 0) CTRL_SetMode (CTRL_AcqOnly);
			else CTRL_SetMode (CTRL_Stop);
		}
	}
	LeaveCritical ();
}


// ===========================================================================
// <TMAIN_Mode>
///
/// \brief	Set the application working mode (stopped, free, equilibrium)
///
/// \param[in]	mode	Application mode
// ===========================================================================
void TMAIN_SetMode (TMAIN_Mode mode)
{
	TLED_Off (LED_GREEN);
	TLED_Off (LED_RED);
	TLED_Off (LED_YELLOW);

	EnterCritical ();
	{	
		gs_mode = mode;
		
		// Configure the controller accordingly
		switch (mode)
		{
		default:
		case MODE_Stop:
			if (gs_tm == 0) CTRL_SetMode (CTRL_Stop);
			else CTRL_SetMode (CTRL_AcqOnly);
			break;
			
		case MODE_Free: 
			CTRL_SetMode (CTRL_Free);
			TLED_On (LED_GREEN);
			break;
			
		case MODE_Control: 
			CTRL_SetMode (CTRL_Control);
			break;
		}	
	}
	LeaveCritical ();
}



// ###########################################################################
//
// P R I V A T E
//
// ###########################################################################

// ===========================================================================
// <InitApplication>
///
/// \brief	Initialize the whole application
///
/// \return	0 in case of success
// ===========================================================================
static Word InitApplication ()
{
	Word error = 0;
	
	// Basic tests and setup
	if (SetupGyroscope () != 0) error = 4;
	else if (SetupAccelerometer () != 0) error = 3;
	else if (TestMotor () != 0) error = 2;
	if (error != 0) return error;
	
	// Restore application settings, if any
	CFG_Restore ();

	// Init our buffer to send the telemetries
	MSG_InitBuffer (&gs_tmBuffer, gs_rawBuffer, sizeof (gs_rawBuffer));
	
	// Everything stopped
	gs_tm = 0;
	gs_saveConfig = False;
	
	// Initialize the Pseudo Random Number Generator
	InitPnrg ();

	// Start the controller
	TMAIN_SetMode (MODE_Control);

	// OK, we release the other tasks
	ResumeTask (g_taskUartTx);
	ResumeTask (g_taskUartRx);
	
	return 0;
}


// ===========================================================================
// <InitPnrg>
///
/// \brief	Initialize the random number generator thanks to the sensors noise
// ===========================================================================
static void InitPnrg ()
{
	Short acc [3];
	
	// Seed the generator with random data
	ADXL345_GetAccelerations (g_ADXL345, acc, acc+1, acc+2);
	PRNG_Seed ((Byte*) acc, sizeof (acc));
}


// ===========================================================================
// <SaveConfig>
///
/// \brief	Save the current configuration in EEPROM
// ===========================================================================
static void SaveConfig ()
{
	gs_saveConfig = False;
	CFG_Save ();
}


// ===========================================================================
// <SendTelemetry>
///
/// \brief	Collect and push all the telemetries through the UART
///
/// \param	cycleCounter		Value of the control process cycle counter
// ===========================================================================
static void SendTelemetry (Dword cycleCounter)
{
	CTRL_Sensors sensors;
	CTRL_State state;
	CTRL_State targetState;
	CTRL_Command command;
	Dword timestamp;

	// Telemetries are sent 1 time out of n
	if (++gs_tmCounter >= gs_tm) gs_tmCounter = 0;
	if (gs_tmCounter != 0) return;
	
	// Get a copy of the last sensor values and pendulum state estimation
	CTRL_GetPendulumSensors (&sensors);
	CTRL_GetPendulumState (&state);
	CTRL_GetPendulumTargetState (&targetState);
	CTRL_GetPendulumCommand (&command);
	timestamp = GetMsCount ();

	// Start of telemetries
	MSG_StartTM (&gs_tmBuffer, "TM.Start");
	MSG_AddParamLong (&gs_tmBuffer, cycleCounter);
	MSG_AddParamLong (&gs_tmBuffer, timestamp);
	MSG_FinishAndSend (&gs_tmBuffer);

	// Send sensors
	MSG_StartTM (&gs_tmBuffer, "SENSORS");
	MSG_AddParamLong (&gs_tmBuffer, sensors.bldcSpeed);
	MSG_AddParamLong (&gs_tmBuffer, sensors.gyroZ);
	MSG_AddParamLong (&gs_tmBuffer, sensors.accXYZ [0]);
	MSG_AddParamLong (&gs_tmBuffer, sensors.accXYZ [1]);
	MSG_AddParamLong (&gs_tmBuffer, sensors.accXYZ [2]);
	MSG_FinishAndSend (&gs_tmBuffer);

	// Send state
	MSG_StartTM (&gs_tmBuffer, "STATE");
	MSG_AddParamLong (&gs_tmBuffer, state.bodyAngle);
	MSG_AddParamLong (&gs_tmBuffer, state.bodySpeed);
	MSG_AddParamLong (&gs_tmBuffer, state.wheelSpeed);
	MSG_AddParamLong (&gs_tmBuffer, targetState.bodyAngle);
	MSG_AddParamLong (&gs_tmBuffer, targetState.bodySpeed);
	MSG_AddParamLong (&gs_tmBuffer, targetState.wheelSpeed);
	MSG_FinishAndSend (&gs_tmBuffer);

	// Send motor command
	MSG_StartTM (&gs_tmBuffer, "CTRL");
	MSG_AddParamLong (&gs_tmBuffer, command.brake? 1:0);
	MSG_AddParamLong (&gs_tmBuffer, command.torque);
	MSG_FinishAndSend (&gs_tmBuffer);

	// End of telemetries
	MSG_StartTM (&gs_tmBuffer, "TM.End");
	MSG_FinishAndSend (&gs_tmBuffer);
}


// ===========================================================================
// <TestMotor>
///
/// \brief	Test if we can drive the motor and get feedback
///
/// \return		0 if successful
// ===========================================================================
static int TestMotor ()
{
	Word speed0, speed1;
	
	// Apply a small torque (5%) on the motor
	MOTOR_RawCommand (MOTOR_Forward, 50);

	// Wait in order to get some speed
	// Measure speed
	SleepTask (DELAY_MS (500));
	speed0 = BSP_BLDCGetSpeed (NULL);

	// Brake, wait and check motor is stopped
	MOTOR_RawCommand (MOTOR_Disabled, 0);
	
	SleepTask (DELAY_MS (1500));
	speed1 = BSP_BLDCGetSpeed (NULL);

	if (speed0 < 300 || speed1 != 0) return -1;
	return 0;
}


// ===========================================================================
// <SetupAccelerometer>
///
/// \brief	Get access to the ADXL345 accelerometers and perform initialization
///
/// \return 0 if successful
// ===========================================================================
static int SetupAccelerometer ()
{
	// Basic setup of the device
	if (ADXL345_Init (g_ADXL345) != 0) return -1;

	// Put the device in normal measurement mode @ 100 samples/s
	ADXL345_SetBaudrate (g_ADXL345, ADXL345_BR_100);	
	ADXL345_SetLowPowerMode (g_ADXL345, 0);
	ADXL345_SetMode (g_ADXL345, ADXL345_MODE_MEASURE);

	return 0;
}


// ===========================================================================
// <SetupGyroscope>
///
/// \brief	Get access to the ISZ2510 Gyro and perform initialization
///
/// \return 0 if successful
// ===========================================================================
static int SetupGyroscope ()
{
	Word d;
	
	// Basic setup of the device
	if (ISZ2510_Init (g_ISZ2510) != 0) return -1;

	// Configure bandwidth and sample rate
	ISZ2510_SetBandwidth (g_ISZ2510, ISZ2510_BW_41);
	d = ISZ2510_SetBaudrate (g_ISZ2510, 50);

	return 0;
}

// End

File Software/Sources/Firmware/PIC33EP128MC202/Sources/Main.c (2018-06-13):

// ###########################################################################
//
// Copyright (C) 2015 GenId SPRL
//
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
/// \file	Main.c
/// \author	Jean-Sebastien Gonsette
/// \date	17/09/2014
///
/// Entry point for iPendulum application. This module loads the configuration,
/// set up the hardware and the OS. Then it launches the different tasks.
// ###########################################################################

#include "Main.h"
#include "Version.h"
#include "BSP.h"
#include "Global.h"
#include "Pendulum.h"
#include "./Interfaces/Battery.h"
#include "./Interfaces/Motor.h"
#include "./Tasks/Controller.h"
#include "./Tasks/TaskUartTx.h"
#include "./Tasks/TaskUartRx.h"
#include "./Tasks/TaskLED.h"
#include "./Tasks/TaskMain.h"


// ===========================================================================
// D E F I N E
// ===========================================================================

// Task priority levels
#define TASK_PRIO_LED           1
#define TASK_PRIO_MAIN          2
#define TASK_PRIO_UART_TX      	3
#define TASK_PRIO_UART_RX      	4


// ===========================================================================
// P R I V A T E 
// ===========================================================================


// ===========================================================================
// P R I V A T E   P R O T O
// ===========================================================================

/// \name Module private functions
//@{
//@}



// ###########################################################################
//
// P U B L I C
//
// ###########################################################################

// ===========================================================================
// <main>
///
/// \brief		Entry point: Set up the hardware, os and application
// ===========================================================================
int main ()
{
	const PDL_Physics* p;

	// Hardware, OS, drivers and devices initialization
	BSP_Init ();

	// Application initialization
	PDL_Init ();
	TUARTRX_Init ();
	TUARTTX_Init ();
	CTRL_Init ();

	// Motor and Battery initialization
	p = PDL_GetPhysics ();

	MOTOR_Init (p->motor.I);
	BAT_Init (BAT_CAPACITY);

	// Create all applicative tasks
	g_taskMain = CreateTask (TMAIN_EntryPoint, "Task_Main", 600, null, TASK_PRIO_MAIN, 0);
	g_taskUartTx = CreateTask (TUARTTX_EntryPoint, "Task_UART_Tx", 500, null, TASK_PRIO_UART_TX, 0);
	g_taskUartRx = CreateTask (TUARTRX_EntryPoint, "Task_UART_Rx", 500, null, TASK_PRIO_UART_RX, 0);
	g_taskLED = CreateTask (TLED_EntryPoint, "Task_LED", 300, null, TASK_PRIO_LED, 0);

	SuspendTask (g_taskUartTx);
	SuspendTask (g_taskUartRx);
	
	// Start OS
	StartKernel ();

    // ...
	// Reset
	__asm__ ("reset");
	return 0;
}



// End

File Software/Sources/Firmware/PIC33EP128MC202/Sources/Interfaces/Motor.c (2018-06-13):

// ###########################################################################
//
// Copyright (C) 2015 GenId SPRL
//
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
#include <math.h>
#include "Debug.h"
#include "BSP.h"
#include "Global.h"
#include "Motor.h"
#include "Pendulum.h"
#include "./Tools/FastTrigo.h"


// ===========================================================================
// D E F I N E
// ===========================================================================


// ===========================================================================
// T Y P E S
// ===========================================================================


// ===========================================================================
// P R I V A T E
// ===========================================================================

/// Calibration values
static MOTOR_CalibValues gs_calib;

/// Stall torque
static float gs_tStall;

/// No load max. speed
static float gs_maxSpeed;

/// Max. torque limit settable to the BLDC controller
static float gs_maxTorqueLimit;

/// Rotor total inertia
static float gs_Iw;


// ===========================================================================
// P R I V A T E   P R O T O
// ===========================================================================

/// \name Internal functions
//@{
static void SetTorqueFromThrottle (float torque, float speed, float inertia, float dt);
static void SetTorqueFromCurrentLimit (float torque, float speed);
static float CalibrateTorqueRequest (float torque, float speed, Bool highMode);
static void RawCommand (MOTOR_Mode mode, Word threshold);
static void SetThrottle (Short throttle);
//@}



// ###########################################################################
//
// P U B L I C
//
// ###########################################################################

// ===========================================================================
// <MOTOR_Init>
///
/// \brief		Initialize the motor properties
///
/// Rotor inertia is used by this module to control motor torque on the basis
/// of speed increment.
///
/// \param	Iw		Rotor total intertia (with load)  [K/m^2]
// ===========================================================================
void MOTOR_Init (float Iw)
{
	// Default, uncalibrated friction curve
	gs_calib.friction_f0 = 0.001f;
	gs_calib.friction_f1 = 9.6e-6f;
	
	gs_calib.calib_high [0].t0_0 = 0.00171f;
	gs_calib.calib_high [0].t0_t = 0.777f;
	gs_calib.calib_high [0].tw_0 = -1.82e-5f;
	gs_calib.calib_high [0].tw_t = 9.97e-4f;

	gs_calib.calib_high [1].t0_0 = 0.00187f;
	gs_calib.calib_high [1].t0_t = 0.709f;
	gs_calib.calib_high [1].tw_0 = 6.89e-6f;
	gs_calib.calib_high [1].tw_t = -0.000686f;

	gs_calib.calib_high [2].t0_0 = -0.00119f;
	gs_calib.calib_high [2].t0_t = 0.799f;
	gs_calib.calib_high [2].tw_0 = -1.598e-5f;
	gs_calib.calib_high [2].tw_t = -0.000885f;

	gs_calib.calib_high [3].t0_0 = 0.00119f;
	gs_calib.calib_high [3].t0_t = 0.905f;
	gs_calib.calib_high [3].tw_0 = -7.98e-6f;
	gs_calib.calib_high [3].tw_t = -0.000393f;

	gs_calib.calib_low [0].t0_0 = 0.00068f;
	gs_calib.calib_low [0].t0_t = 0.5839f;
	gs_calib.calib_low [0].tw_0 = -2.887e-6f;
	gs_calib.calib_low [0].tw_t = 0.00134f;

	gs_calib.calib_low [1].t0_0 = -5.547e-5f;
	gs_calib.calib_low [1].t0_t = 0.795f;
	gs_calib.calib_low [1].tw_0 = 1.131e-5f;
	gs_calib.calib_low [1].tw_t = 0.00156f;

	gs_calib.calib_low [2].t0_0 = -0.000403f;
	gs_calib.calib_low [2].t0_t = 0.67008f;
	gs_calib.calib_low [2].tw_0 = 2.63e-6f;
	gs_calib.calib_low [2].tw_t = -5.11e-5f;

	gs_calib.calib_low [3].t0_0 = -3.189e-6f;
	gs_calib.calib_low [3].t0_t = 0.7937f;
	gs_calib.calib_low [3].tw_0 = 1.059e-5f;
	gs_calib.calib_low [3].tw_t = -0.00162f;

	gs_tStall = (float) MOTOR_STALL_TORQUE / 1000.0f;
	gs_maxSpeed = RPM (MOTOR_FULL_SPEED);
	gs_maxTorqueLimit = (float) MOTOR_MAX_TORQUE_LIMIT / 1000.0f;
	
	gs_Iw = Iw;
}


// ===========================================================================
// <MOTOR_GetFriction>
///
/// \brief	Return the motor friction torque for a given rotation speed.
///
/// \param 	w	Rotor angular speed [rad/s]
///
/// \return	Friction torque [N.m].
///			<0 when wheel goes forward.
///			>0 when wheel goes backward
// ===========================================================================
float MOTOR_GetFriction (float w)
{
	float f;

	// Negative friction if speed is positive
	if (w >= 0.0f) f = -(gs_calib.friction_f1*w + gs_calib.friction_f0);
	
	// Positive friction in the other case
	else f = -(gs_calib.friction_f1*w - gs_calib.friction_f0);
	
	return f;
}


// ===========================================================================
// <MOTOR_GetBrakingTorque>
///
/// \brief	Return the motor braking torque for a given rotation speed.
///
/// \param 	w	Rotor angular speed [rad/s]
///
/// \return	Braking torque [N.m].
///			<0 when wheel goes forward.
///			>0 when wheel goes backward
// ===========================================================================
float MOTOR_GetBrakingTorque (float w)
{
	Bool neg;
	float bTrq;

	// Torque sign depends on speed direction
	neg = (w <= 0.0f ? True : False);
	if (w <= 0.0f) w = -w;
	
	// Get torque from speed
	bTrq = gs_tStall * w / gs_maxSpeed;
	if (bTrq > 0.100f) bTrq = 0.100f;
	
	// Set torque sign
	if (neg == False) bTrq = -bTrq;
	
	return bTrq;
}


// ===========================================================================
// <MOTOR_GetFriction>
///
/// \brief	Return the motor speed needed to achieve a given friction torque
///
/// \param 	torque	Friction torque [N.m]
///
/// \return	Motor speed [rad/s].
///			>0 when wheel goes forward (negative torque).
///			<0 when wheel goes backward (positive torque)
// ===========================================================================
float MOTOR_GetFrictionSpeed (float torque)
{
	float w;
	Bool neg = False;
	
	if (torque < 0.0f) 
	{
		torque = -torque;
		neg = True;
	}
	
	// Null speed if torque below stall friction
	if (torque <= gs_calib.friction_f0) return 0.0f;
	
	// Inverse friction law
	torque -= gs_calib.friction_f0;
	w = -torque / gs_calib.friction_f1;
	
	if (neg) w = -w;
	return w;
}
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

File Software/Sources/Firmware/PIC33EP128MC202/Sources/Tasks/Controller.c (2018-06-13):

// ###########################################################################
//
// Copyright (C) 2015 GenId SPRL
//
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
#include "Version.h"
#include "BSP.h"
#include "Global.h"
#include "Debug.h"
#include "Controller.h"
#include "Pendulum.h"
#include "TaskLED.h"
#include "./Devices/ADXL345.h"
#include "./Devices/ISZ2510.h"
#include "./Algorithms/KalmanFree.h"
#include "./Algorithms/CtrlJump.h"
#include "./Algorithms/CtrlFall.h"
#include "./Algorithms/CtrlEquilibrium.h"
#include "./Algorithms/Trajectory.h"
#include "./Interfaces/Motor.h"
#include "./Tools/FastTrigo.h"
#include "./Tools/PRNG.h"


// ===========================================================================
// D E F I N E
// ===========================================================================

/// Controller period [ms]
#define PERIOD		10

/// Time to wait to consider the pendulum is still [s]
#define STILL_DELAY		4

/// Max angle the pendulum can move when it is considered to be still [°]
#define STILL_MAX_MOVE	1.0f

/// Minimum swing amplitude [deg]
#define SWING_AMPL_MIN	4

/// Maximum swing amplitude [deg]
#define SWING_AMPL_MAX	6

/// Minimum swing periodicity [ms]
#define SWING_PER_MIN		1000

/// Maximum swing amplitude [ms]
#define SWING_PER_MAX		1200


// ===========================================================================
// T Y P E S
// ===========================================================================

/// Data for 'still' state identification
typedef struct
{
	unsigned int stillCount;
	float angle;
}
Still;


/// Controller actions when pendulum is under control
typedef enum
{
	ST_Wait,			///< Wait pendulum is still
	ST_Jump,			///< Jumping
	ST_Move,			///< Equilibrium and/or move
	ST_Fall				///< Fall on the ground
}
E_CtrlAction;


/// Movement set when pendulum is in equilibrium
typedef enum
{
	MOVE_Still,			///< Simple equilibrium
	MOVE_Swing			///< Swinging
}
E_CtrlMovement;


/// Control management structure
typedef struct
{
	CTRL_Mode mode;			///< Controller mode
	E_CtrlAction action;	///< Controller action when pendulum is under control
	E_CtrlMovement movment;	///< Controller movement when pendulum is in equilibrium
	Word nextMoveTime;		///< Time left before next movement [ms]
	Word nextFallTime;		///< Time left before falling [ms]
		
	CTRL_State targetState;	///< Pendulum target state (for trajectory)
	CTRL_State state;		///< Pendulum state estimation
	CTRL_Command command;	///< Command to drive the motor
	CTRL_Sensors sensors;	///< Sensor values
}
Control;


// ===========================================================================
// P R I V A T E
// ===========================================================================

/// Cycle count
static Dword gs_cycleCount;

/// Control management
static Control gs_control;


/// Periodic timer for controller processing
static HANDLE gs_timer;

/// Event for cycle signalisation
static HANDLE gs_event;


/// Still estimation
static Still gs_stillEval;

/// Counter for wheel speed update
static Word gs_wheelCounter;

/// Counter for verticality check
static Word gs_verticalCounter;

/// Counter to wait for kalman stabilization at startup
static Word gs_initCounter;



// ===========================================================================
// P R I V A T E   P R O T O
// ===========================================================================

/// \name Internal functions
//@{
static void TimerProcess (void* param);
static void DriveMotor (CTRL_State state, CTRL_Command command);
static CTRL_State ObserverProcess (CTRL_Sensors sensors, CTRL_Command command, Word wheelCounter);
static CTRL_Command ControlProcess (CTRL_State state, CTRL_State *targetState);
static CTRL_Command StopMotor (Short rpm);

static void GoWait ();
static void GoJump ();
static void GoFall ();
static void GoEquilibrium ();
static void SelectNextMovement ();

static Bool IsStill (CTRL_State state);

static Short ComputeVerticality (CTRL_Sensors sensors);
//@}



// ###########################################################################
//
// P U B L I C
//
// ###########################################################################

// ===========================================================================
// <CTRL_Init>
///
/// \brief		Initialize the controller module
// ===========================================================================
void CTRL_Init ()
{
	gs_control.mode = CTRL_Stop;
	gs_cycleCount = 0;
	gs_initCounter = 1000/PERIOD;
	
	// Initialize the different algorithms
	KFREE_Init ();
	
	// Periodic timer for controller processing
	// Event for processing signalisation
	gs_timer = CreateTimer (TimerProcess, TM_PERIODIC, DELAY_MS (PERIOD));
	gs_event = CreateEvent ();
}


// ===========================================================================
// <CTRL_SetMode>
///
/// \brief	Set the controller working mode (stopped, acq only, free, controlling)
///
/// \param[in]	mode	Controller mode
// ===========================================================================
void CTRL_SetMode (CTRL_Mode mode)
{
	EnterCritical ();
	{
		// Save mode and start the timer if needed
		gs_control.mode = mode;
		if (gs_control.mode != CTRL_Stop) StartTimer (gs_timer, null);
		else 
		{
			gs_cycleCount = 0;
			StopTimer (gs_timer, TM_SIG_NOT);
			MOTOR_RawCommand (MOTOR_Disabled, 0);
		}
		
		// First state when pendulum is under control
		if (gs_control.mode == CTRL_Control) GoWait ();
		
		// No command to the motor by default
		gs_control.command.torque = 0;
		gs_control.command.brake = False;
		gs_control.command.end = False;
	}
	LeaveCritical ();
}


// ===========================================================================
// <CTRL_WaitCycle>
///
/// \brief	Wait for the end of the next controller cycle
///
/// \param[in]	timeout		Timeout for waiting
/// \param[out]	pCount		Cycle counter
///
/// \return		False if timeout expired before next cycle comes
// ===========================================================================
Bool CTRL_WaitCycle (Long timeout, Dword *pCount)
{
	// Wait the event get signalized
	if (WaitEventTo (gs_event, EV_WAIT_ANY, EV_NO_RESET, 0x01, timeout) == 0x01) 
	{
		*pCount = gs_cycleCount;
		return True;
	}
	
	*pCount = 0;	
	return False;
}
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

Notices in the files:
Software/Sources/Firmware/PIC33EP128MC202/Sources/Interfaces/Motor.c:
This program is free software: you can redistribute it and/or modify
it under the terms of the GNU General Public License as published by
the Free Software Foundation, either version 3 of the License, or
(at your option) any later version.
